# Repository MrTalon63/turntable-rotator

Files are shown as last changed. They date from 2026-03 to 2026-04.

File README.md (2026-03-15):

# Turntable Rotator

## tl;dr

- In theory amazing azimuth control step resolution of 0.02 degrees
- All parts can be 3D printed
- Uses off the shelf NEMA 17 stepper motors and drivers
- Multi-use architecture:tm:
- Universal controller board that can be used for other projects as well

In a nutshell, this project is a simple antenna rotator (could be used for photogrammetry?) that uses a belt driven turntable to rotate the azimuth of the antenna.
Elevation has not been implemented yet, but thanks to modular design you can mount an antenna on the turntable and use it as a simple rotator for azimuth only, attach fixed elevation antennas, or just slap an elevation mechanism on top of the turntable and use it as a full azimuth/elevation rotator.

### Electronics

The controller board is powered by an ESP32-S3 module, can be powered with any 9 - 40 VDC power source and supports two stepper motors and three limit switches.
You can also use servo for elevation instead, there's a pinout for that, need to supply your own power for the servo though.
The board has a USB-C port for programming and debugging.

### Software

SOFTWARE IS NOT YET IMPLEMENTED!!!
~~Commands can be sent over WiFi or UART, and the board can be configured as a WiFi access point or connect to an existing WiFi network.
The board also has a built in web server that can be used to for control, calibration and configuration, but that is also not implemented yet.~~

### Mechanical

First of all, I'm not nowhere competent in mechanical design, this is my first attempt at designing something like this, so if you have any suggestions or improvements please let me know.

The turntable is belt driven, with a 20 tooth pulley on the motor and a 120 tooth pulley on the turntable, giving a 6:1 gear ratio, which means that with a 400 step/rev (0.9 degree/step) stepper motor, we get a theoretical step resolution of 0.02 degrees, which is pretty good for a rotator of this size.
The turntable is suppported by a chungus 6910 bearing, which also allows for cable passage through the center of the turntable.

The turntable is designed to be 3D printed, and all parts can be printed on a standard 3D printer. Due to my lack of design skills, you'd want pretty accurate printer, as the tolerances can get pretty tight, especially for the bearing and screw holes.

### Future Work

- [ ] Redesign the turntable, it was the first part I designed and it shows, the Fusion timeline is a mess and a single change just breaks everything.
- [ ] Design an elevation mechanism, maybe a simple belt driven one, or maybe a servo driven one, not sure yet.
- [ ] Implement the software, need working PCB first.
- [ ] Design pole mount, maybe a simple clamp on design, or maybe a tripod mount, not sure yet.

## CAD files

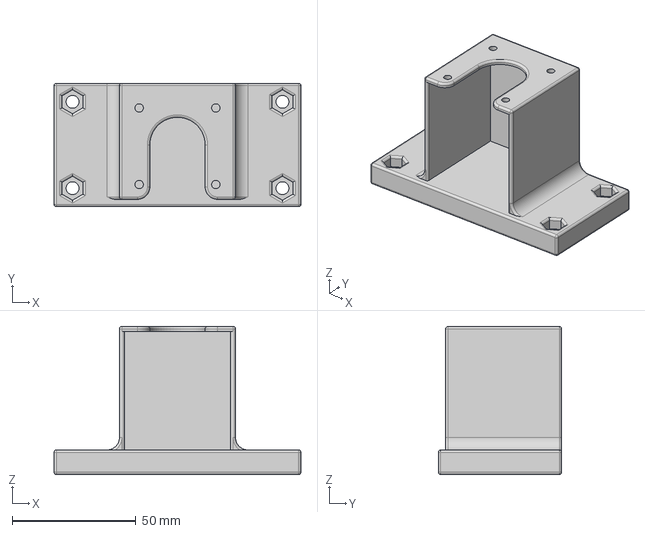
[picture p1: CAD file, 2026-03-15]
parts/STEP/stepper_mount.step
100.0 x 50.0 x 60.0 mm

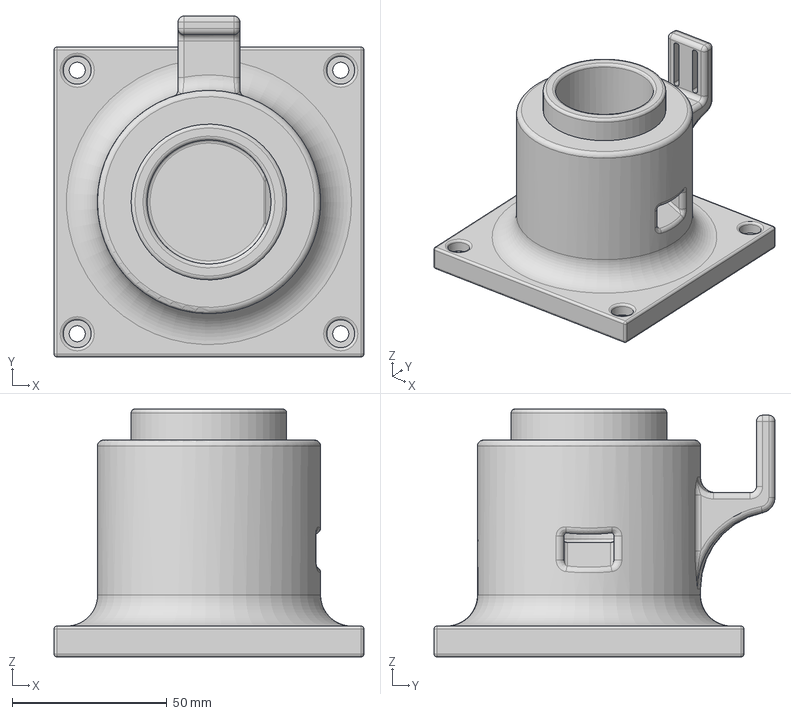
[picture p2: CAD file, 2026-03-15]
parts/STEP/turntable_base.step
100.0 x 110.0 x 80.0 mm

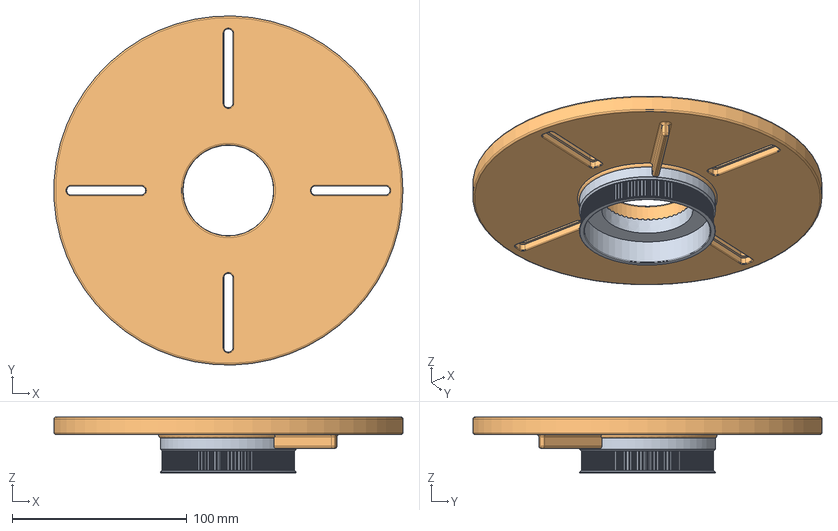
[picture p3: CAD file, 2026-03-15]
parts/STEP/turntable.step
199.8 x 199.9 x 32.0 mm

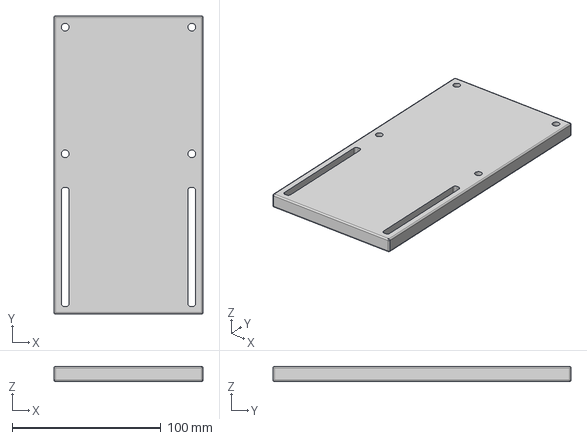
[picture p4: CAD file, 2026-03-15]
parts/STEP/baseplate.step
100.0 x 200.0 x 10.0 mm

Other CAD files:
parts/F3D/baseplate.f3d
parts/F3D/stepper_mount.f3d
parts/F3D/turntable.f3d
parts/F3D/turntable_base.f3d

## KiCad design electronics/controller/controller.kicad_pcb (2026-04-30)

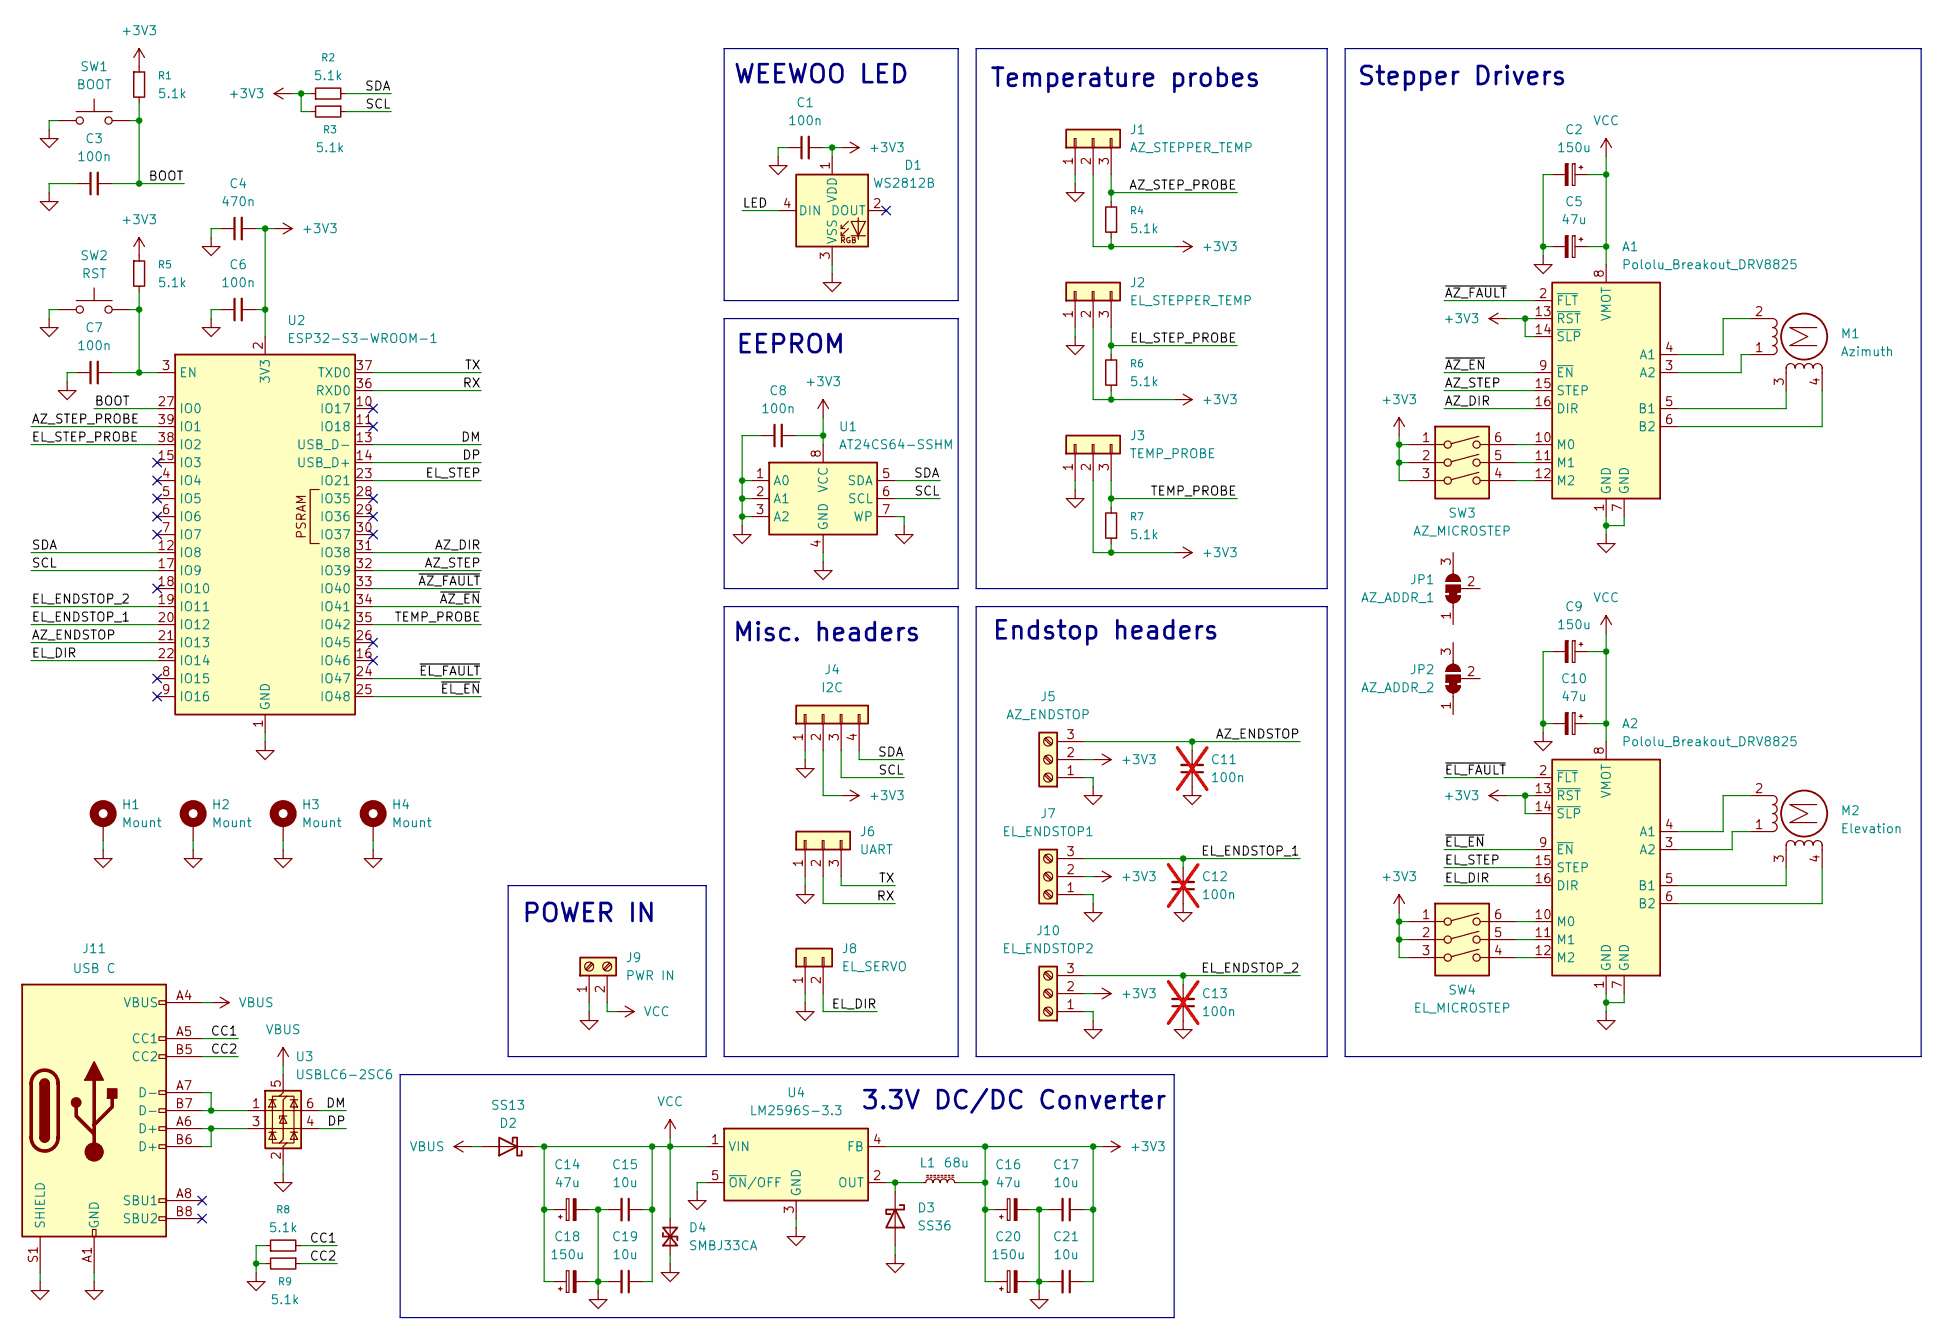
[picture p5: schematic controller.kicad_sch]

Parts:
A1, A2: Pololu_Breakout_DRV8825; Pololu_Breakout-16_15.2x20.3mm
C1, C3, C6, C7, C8: 100n; C_0402_1005Metric
C2, C9, C18, C20: 150u; CP_Elec_10x10
C4: 470n; C_0402_1005Metric
C5, C10, C14, C16: 47u; CP_Elec_8x10
C11, C12, C13: 100n; C_0603_1608Metric_Pad1.08x0.95mm_HandSolder; not fitted
C15, C17, C19, C21: 10u; C_1210_3225Metric
D1: WS2812B; LED_WS2812B_PLCC4_5.0x5.0mm_P3.2mm
D2: SS13; D_SMA
D3: SS36; D_SMA
D4: SMBJ33CA; D_SMB
H1, H2, H3, H4: Mount; MountingHole_2.7mm_M2.5_DIN965_Pad
J1: AZ_STEPPER_TEMP; PinHeader_1x03_P2.54mm_Vertical
J2: EL_STEPPER_TEMP; PinHeader_1x03_P2.54mm_Vertical
J3: TEMP_PROBE; PinHeader_1x03_P2.54mm_Vertical
J4: I2C; PinHeader_1x04_P2.54mm_Vertical
J5: AZ_ENDSTOP; TerminalBlock_MaiXu_MX126-5.0-03P_1x03_P5.00mm
J6: UART; PinHeader_1x03_P2.54mm_Vertical
J7: EL_ENDSTOP1; TerminalBlock_MaiXu_MX126-5.0-03P_1x03_P5.00mm
J8: EL_SERVO; PinHeader_1x02_P2.54mm_Vertical
J9: PWR IN; TerminalBlock_MaiXu_MX126-5.0-02P_1x02_P5.00mm
J10: EL_ENDSTOP2; TerminalBlock_MaiXu_MX126-5.0-03P_1x03_P5.00mm
J11: USB C; USB_C_Receptacle_GCT_USB4105-xx-A_16P_TopMnt_Horizontal
JP1: AZ_ADDR_1; SolderJumper-3_P1.3mm_Bridged12_RoundedPad1.0x1.5mm_NumberL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
JP2: AZ_ADDR_2; SolderJumper-3_P1.3mm_Bridged12_RoundedPad1.0x1.5mm_NumberL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
L1: 68u; L_Coilcraft_MSS1260-XXX
M1: Azimuth; TerminalBlock_MaiXu_MX126-5.0-04P_1x04_P5.00mm
M2: Elevation; TerminalBlock_MaiXu_MX126-5.0-04P_1x04_P5.00mm
R1, R2, R3, R4, R5, R6, R7, R8, R9: 5.1k; R_0402_1005Metric
SW1: BOOT; KLS7TS6611
SW2: RST; KLS7TS6611
SW3: AZ_MICROSTEP; SW_DIP_SPSTx03_Slide_KingTek_DSHP03TJ_W5.25mm_P1.27mm_JPin
SW4: EL_MICROSTEP; SW_DIP_SPSTx03_Slide_KingTek_DSHP03TJ_W5.25mm_P1.27mm_JPin
U1: AT24CS64-SSHM; TSSOP-8_4.4x3mm_P0.65mm
U2: ESP32-S3-WROOM-1
U3: USBLC6-2SC6; SOT-23-6
U4: LM2596S-3.3; TO-263-5_TabPin3

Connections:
/AZ_DIR: A1.16 (DIR), U2.31 (IO38)
/AZ_ENDSTOP: C11.2, J5.3, U2.21 (IO13)
/AZ_STEP: A1.15 (STEP), U2.32 (IO39)
/AZ_STEP_PROBE: J1.3, R4.2, U2.39 (IO1)
/BOOT: C3.2, R1.2, SW1.2, U2.27 (IO0)
/CC1: J11.A5 (CC1), R8.2
/CC2: J11.B5 (CC2), R9.1
/DM: U2.13 (USB_D-), U3.6 (I/O1)
/DP: U2.14 (USB_D+), U3.4 (I/O2)
/EL_DIR: A2.16 (DIR), J8.2, U2.22 (IO14)
/EL_ENDSTOP_1: C12.2, J7.3, U2.20 (IO12)
/EL_ENDSTOP_2: C13.2, J10.3, U2.19 (IO11)
/EL_STEP: A2.15 (STEP), U2.23 (IO21)
/EL_STEP_PROBE: J2.3, R6.2, U2.38 (IO2)
/LED: D1.4 (DIN)
/RX: J6.2, U2.36 (RXD0)
/SCL: J4.3, R3.1, U1.6 (SCL), U2.17 (IO9)
/SDA: J4.4, R2.2, U1.5 (SDA), U2.12 (IO8)
/TEMP_PROBE: J3.3, R7.2, U2.35 (IO42)
/TX: J6.3, U2.37 (TXD0)
/~AZ_EN: A1.9 (~EN), U2.34 (IO41)
/~AZ_FAULT: A1.2 (~FLT), U2.33 (IO40)
/~EL_EN: A2.9 (~EN), U2.25 (IO48)
/~EL_FAULT: A2.2 (~FLT), U2.24 (IO47)
unnamed: A1.4 (A1), M1.2 (-)
unnamed: A1.3 (A2), M1.1
unnamed: A1.5 (B1), M1.3
unnamed: A1.6 (B2), M1.4
unnamed: A1.10 (M0), SW3.6
unnamed: A1.11 (M1), SW3.5
unnamed: A1.12 (M2), SW3.4
unnamed: A2.4 (A1), M2.2 (-)
unnamed: A2.3 (A2), M2.1
unnamed: A2.5 (B1), M2.3
unnamed: A2.6 (B2), M2.4
unnamed: A2.10 (M0), SW4.6
unnamed: A2.11 (M1), SW4.5
unnamed: A2.12 (M2), SW4.4
unnamed: D3.1 (K), L1.1, U4.2 (OUT)
unnamed: J11.A6 (D+), J11.B6 (D+), U3.3 (I/O2)
unnamed: J11.A7 (D-), J11.B7 (D-), U3.1 (I/O1)
unnamed: C7.2, R5.2, SW2.2, U2.3 (EN)
VBUS: D2.2 (A), J11.A4 (VBUS), J11.A9 (VBUS), J11.B4 (VBUS), J11.B9 (VBUS), U3.5 (VBUS)

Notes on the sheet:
EEPROM
Endstop headers
3.3V DC/DC Converter
Misc. headers
POWER IN
Stepper Drivers
WEEWOO LED
Temperature probes

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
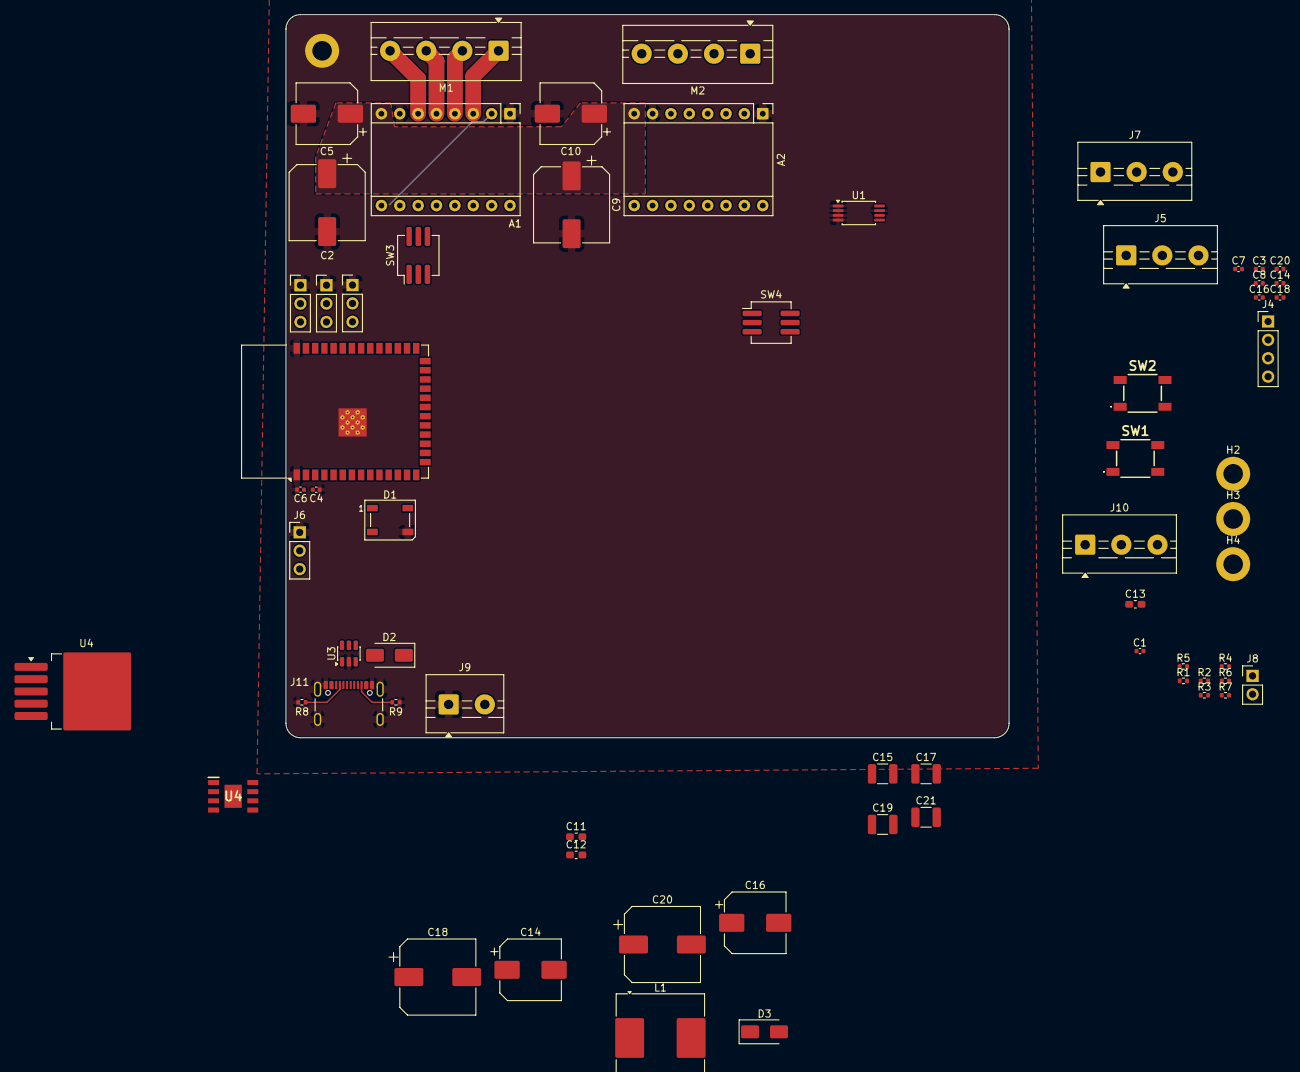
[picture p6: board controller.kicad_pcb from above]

Board: 2 copper layers, 100.0 x 100.0 mm, 66 parts (0 on the bottom side), 45 nets.

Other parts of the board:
C14#2: 47u; CP_Elec_8x10
C16#2, C20#2: 100n; C_0402_1005Metric
C18#2: 150u; CP_Elec_10x10
U4#2: BD433S5EFJ-CE2; SOIC127P600X100-9N

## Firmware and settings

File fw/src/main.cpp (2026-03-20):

#include <Arduino.h>
#include <FastAccelStepper.h>
#include <TMCStepper.h>

#define AZ_DIR_PIN 5
#define AZ_STEP_PIN 6
#define AZ_EN_PIN 2137
#define AZ_CS_PIN 2137
#define R_SENSE 0.11f // Idfk that's what is in example

TMC2130Stepper azDriver(AZ_CS_PIN, R_SENSE);
FastAccelStepperEngine engine = FastAccelStepperEngine();
FastAccelStepper *azStepper = NULL;

void setup() {
  Serial.begin(115200);
  delay(5000); // Wait for USB Serial because it sucky
  Serial.println("Setting up...");
  Serial.println("ESP SDK version: " + String(esp_get_idf_version()));

  SPI.begin();
  azDriver.begin();
  azDriver.toff(5);
  azDriver.rms_current(600); // mA
  azDriver.microsteps(16);

  // Enable sum fancy shit, allegedly stepper should be silky smooth
  azDriver.en_pwm_mode(true);
  azDriver.pwm_autoscale(true);

  engine.init();
  Serial.println("Engine initialized.");
  azStepper = engine.stepperConnectToPin(AZ_STEP_PIN, DRIVER_I2S_DIRECT);

  if (azStepper) {
    Serial.println("Stepper connected to pin.");
  } else {
    Serial.println("Failed to connect stepper to pin.");
    while (1); // Halt execution
  }

  azStepper->setDirectionPin(AZ_DIR_PIN);
  azStepper->setSpeedInUs(10);
  azStepper->setAcceleration(1000);
}

void loop() {
  if (Serial.available()) {
    String input = Serial.readStringUntil('\n');
    input.trim();
    int space = input.indexOf(' ');
    String command;
    String value;
    if (!space) {
      command = input; //no val
      value = "";
    } else {
      command = input.substring(0, space);
      value = input.substring(space + 1);
      value.trim();
    }
    command.toLowerCase();

    if (command == "f" || command == "forward") {
      if (value.isEmpty()) {
        Serial.println("Moving forward...");
        azStepper->runForward();
      } else {
        uint32_t steps = value.toInt();
        Serial.println("Moving forward " + String(steps) + " steps...");
        azStepper->move(steps);
      }

    } else if (command == "b" || command == "backward") {
      if (value.isEmpty()) {
        Serial.println("Moving backward...");
        azStepper->runBackward();
      } else {
        uint32_t steps = value.toInt();
        Serial.println("Moving backward " + String(steps) + " steps...");
        azStepper->move(-steps);
      }

    } else if (command == "s" || command == "speed") {
      if (value.isEmpty()) {
        Serial.println("Current speed: " + String(azStepper->getCurrentSpeedInUs()) + " us/step.");
      } else {
        uint32_t speed = value.toInt();
        azStepper->setSpeedInUs(speed);
        Serial.println("Speed set to " + String(speed) + " us/step.");
      }

    } else if (command == "a" || command == "acceleration") {
      if (value.isEmpty()) {
        Serial.println("Current acceleration: " + String(azStepper->getAcceleration()) + " steps/s^2.");
      } else {
        uint32_t accel = value.toInt();
        azStepper->setAcceleration(accel);
        Serial.println("Acceleration set to " + String(accel) + " steps/s^2.");
      }

    } else if (command == "l" || command == "stop") {
      Serial.println("Stopping...");
      azStepper->stopMove();

    } else if (command == "status") {
      Serial.println("Current status:");
      Serial.println("  Speed: " + String(azStepper->getCurrentSpeedInUs()) + " us/step");
      Serial.println("  Acceleration: " + String(azStepper->getAcceleration()) + " steps/s^2");
      Serial.println("  Current position: " + String(azStepper->getCurrentPosition()) + " steps");
    
    } else if (command == "h" || command == "help") {
      Serial.println("Available commands:");
      Serial.println("  f [steps] - Move forward (optional steps)");
      Serial.println("  b [steps] - Move backward (optional steps)");
      Serial.println("  s [speed] - Set speed in us/step or get current speed");
      Serial.println("  a [accel] - Set acceleration in steps/s^2 or get current acceleration");
      Serial.println("  l         - Stop movement");
      Serial.println("  status    - Show current status");
      Serial.println("  h         - Show this help message");
    }

    else {
      Serial.println("Unknown command: " + command);
    }
  }
}

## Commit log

2026-03-15 Finished controller schematic
    [controller.kicad_pcb, controller.kicad_sch]
2026-03-15 Add Fusion files
    [baseplate.f3d, baseplate.step, stepper_mount.f3d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]
2026-03-15 Switch to Buck converter
    [controller.kicad_sch]
2026-03-18 Add mounting holes to the schematic
    [controller.kicad_sch]
